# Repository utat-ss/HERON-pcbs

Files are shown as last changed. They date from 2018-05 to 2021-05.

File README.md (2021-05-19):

# Printed Circuit Boards (PCBs)

This repository houses Altium PCB designs for the Heron MK II CubeSat project. It contains [pcbs-common](https://github.com/HeronMkII/pcbs-common) as a Git submodule with commonly used schematics.

**Export all schematics and board layouts to PDF files so others can easily view them without using Altium.**

## How to add pcbs-common files into your current Altium project

- Update your GitHub with the pcbs-common submodule

- Run these git commands from your `./pcbs` folder:

```
git submodule init .
git submodule update --remote pcbs-common
```

- Get the files in your current project
- Project → Add Existing to Project → navigate to your copy of pcbs-common → select relevant files for your design.
- Substitute your current subsheets with the pcbs-common versions
- Open properties of target subsheet (the green box) → find the label indicating from where it’s taking the current subsheet → select the ... → navigate to the pcbs-common version in your project → select and OK
- Synchronize the labels to the subsheet with pcbs-common version
- Right click on the green box → sheet actions → synchronize sheet labels → select the pairs of corresponding sheet symbols → select the bottom arrow option (symbol of a beige box to a blue box [this pushes the version from pcbs-common onto the upper level]).
- When you run out of things to link, select the remaining items in the middle column → add (bottom option) → add no ERCs (X symbols) to pins you are not currently using.

## Updating pcbs-common

From the `pcbs` folder:

`$ git submodule update --remote`

This will fetch the latest commit of `pcbs-common` and update your files.

If you get an error about having modified files inside the `pcbs-common` folder, run the following:

```
$ cd pcbs-common
$ git reset --hard
```

This will discard all local changes you have made in the `pcbs-common` folder. Then, run `$ git submodule update --remote` again to download the most updated version of the `pcbs-common` files.

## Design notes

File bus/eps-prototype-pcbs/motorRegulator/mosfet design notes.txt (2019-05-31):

Vds max = 130 V (must be larger than Vout)
Ids max = 8 A
Rds max = 16.25 ohms
"In most applications, a logic level MOSFET can be used"

The critical parameters for selecting a MOSFET are:
1. Minimum threshold voltage, VTH(MIN)
2. On-resistance, RDS(ON)
3. Total gate charge, Qg
4. Reverse transfer capacitance, CRSS
5. Maximum drain to source voltage, VDS(MAX)

*The off-state voltage of the MOSFET is approximately equal to the output voltage*. Vds(max) must be greater
than the output voltage. The power losses in the MOSFET can be categorized into conduction losses and
switching losses

"The voltage on the drive pin, VDR is equal to the input voltage when input voltage is less than 7.2 V. 
VDR is equal to 7.2 V when the input voltage is greater than or equal to 7.2 V"

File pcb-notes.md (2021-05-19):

## Current PCBs in Lab (as of 2019-01-19)

### PAY-SSM

[Manufacturing notes](https://github.com/HeronMkII/pcbs/issues/14)

Programming PAY-SSM microcontroller:
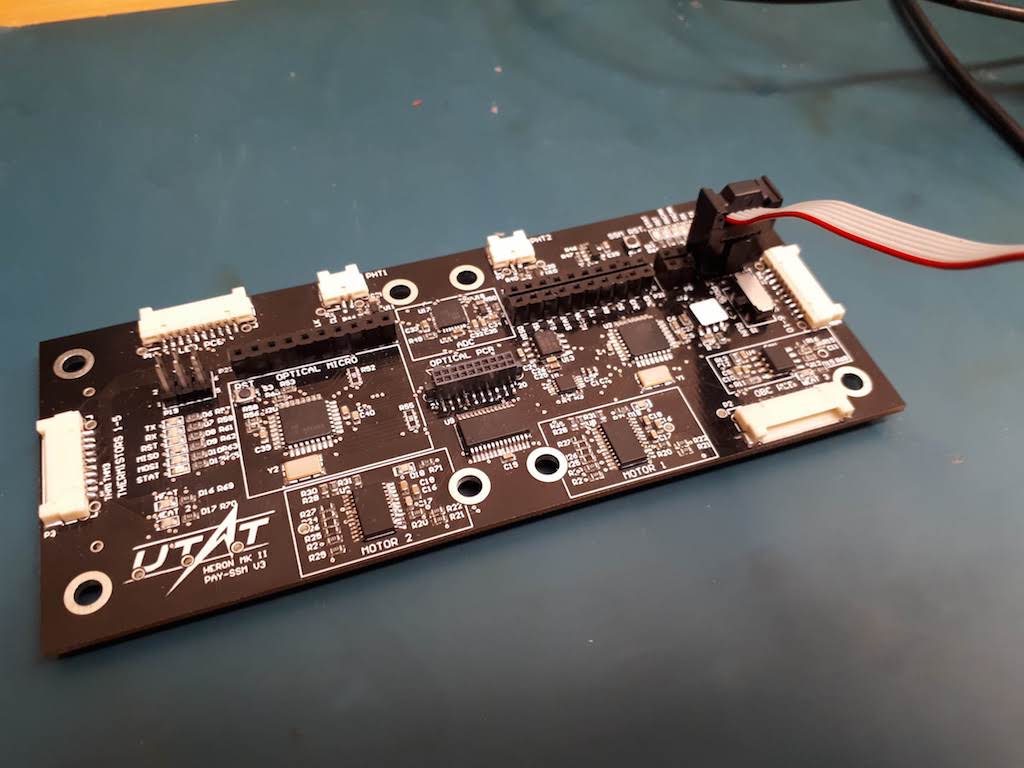
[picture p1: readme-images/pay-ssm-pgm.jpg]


Programming PAY-Optical microcontroller:
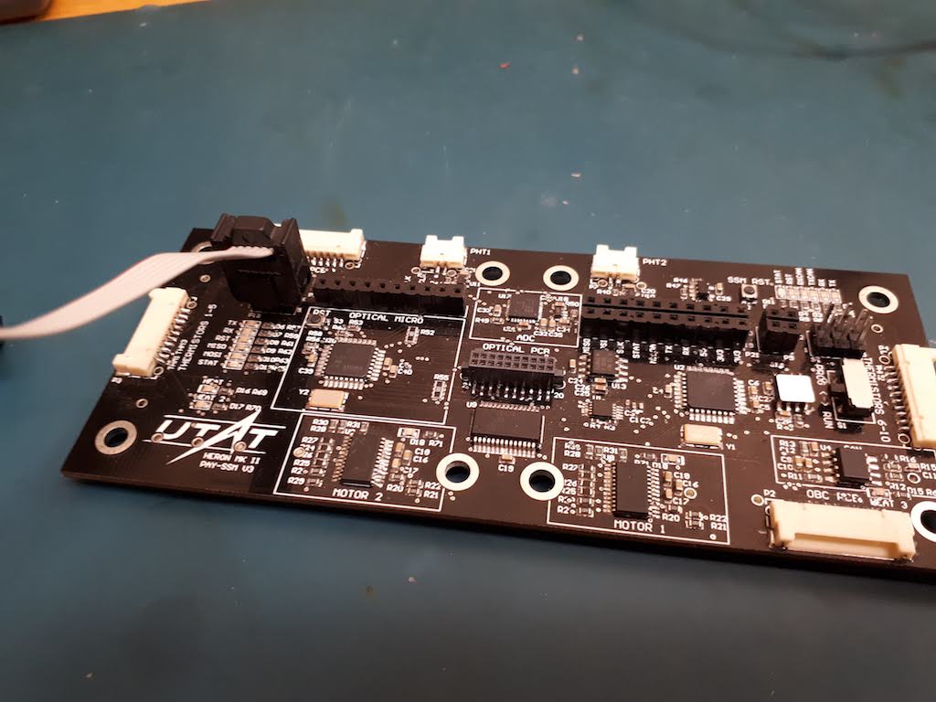
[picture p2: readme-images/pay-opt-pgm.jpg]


- **Programming headers - for both, the notch on the connector must face DOWN**
    - Board orientation is determined by the UTAT logo
- **Contains two microcontrollers:**
    - **PAY-SSM (right side)**
        - Controls SSM functions
        - Need to set switch to PROG when uploading programs, and RUN when executing programs
        - Switch must be in RUN mode for SSM_RST button and UART to work
        - Can leave microcontroller's RX pin connected when uploading a program (commands from a laptop)
    - **PAY-Optical (left side)**
        - Controls optical sensor setup
        - Should be on the PAY-Optical board, but is on the SSM board due to space constraints
        - UART headers (from MCU's perspective) - TX (DI, for printing, more common), RX (CLK, for commands, less common)
        - Need to disconnect RX (CLK) pin when uploading a program
- Payload subsystem main board
- Controls motors, heaters, thermistors
- Interfaces with EPS/OBC on the CAN bus
- 10-pin DF-14 connector to EPS
- 2x2 header on right side between long debugging header and programming header - top 2 pins are MCU's TX (prints), bottom 2 pins are MCU's RX (laptop commands)
- Careful of different 5V and 3V3 headers!!
- 5V supply required if using motors and heaters
- The two microcontrollers are connected to each other over SPI, where PAY-SSM functions as the master and PAY-Optical functions as the slave
- If the PAY-Optical MCU doesn't program properly, the PAY-SSM MCU might be interfering by sending SPI messages to it - either upload an empty program to the PAY-SSM MCU or hold down the SSM_RST button when programming the PAY-Optical MCU
- Disconnected (desoldered) CONFIG pin on both motor drivers so they use phase/enable mode

### PAY-Optical

[Manufacturing notes](https://github.com/HeronMkII/pcbs/issues/15)

Connecting PAY-SSM PCB to PAY-Optical PCB (if using 20-pin cable for debugging instead of stacking header pins):
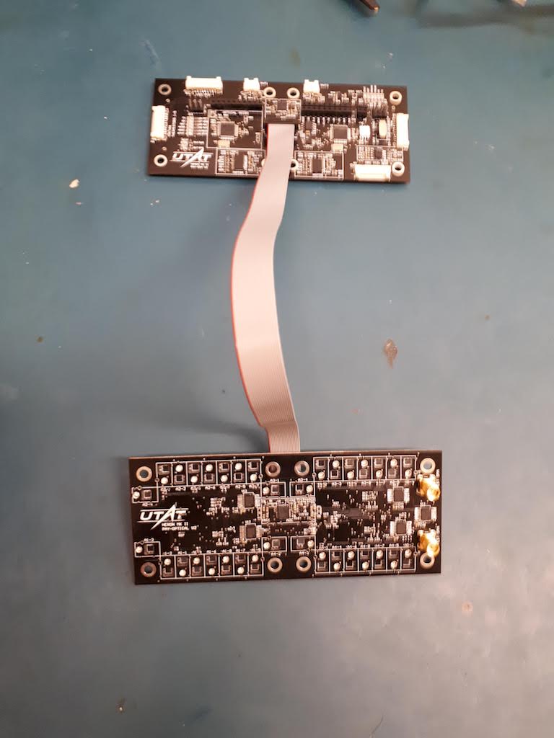
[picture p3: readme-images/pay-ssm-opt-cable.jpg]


- Payload optical board
- Physically stacked on top of PAY-SSM with a 20-pin header
    - Bought a 20-pin wire for testing without having to stack the boards
- 34 optical sensors and 2 SMA connectors to test input by simulating the input signal after the first amplification stage
- MCU for optical setup is located on the PAY-SSM PCB

### PAY-LED

[Manufacturing notes](https://github.com/HeronMkII/pcbs/issues/20)

- Payload LED board
- Contains LEDs on opposite side from PAY-Optical board
- Second copy currently (on 2018-09-18) being soldered by Cindy
- Each LED board has a 10-pin DF14 connector to PAY-SSM

### BUS (OBC/EPS/COMM)

- Combined onboard computer, electrical power systems, and communications on the same board
- Next iteration will have OBC on its own board, EPS/COMM still together on the other board
- Decided to not finish soldering a complete board with all components, just a couple of partially finished boards
- Connects to systems PCB with DSUB-25 connector
- Two MCUs: EPS and OBC
- Must program MCUs through the systems debug PCB

### Systems Debug PCB

- Systems debugging board
- Connects to EPS board with DSUB-25 connector
- Will allow us to plug in the single DSUB-25 cable to the satellite, program and view UART from any board/MCU, and monitor high-level debugging signals
- The following picture shows the v1 (on the left) and v2 (on the right) Systems Debug PCB. V2 has all the components soldered on and is ready to be used. Potential issues and changes are documented in Issue [#70](https://github.com/HeronMkII/pcbs/issues/70)
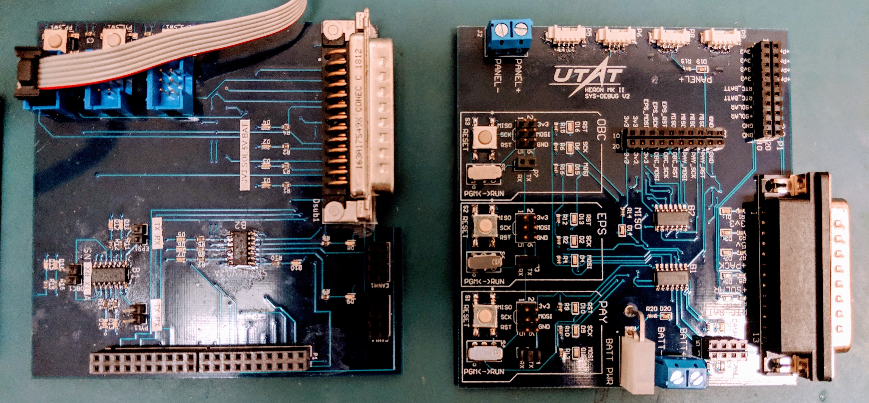
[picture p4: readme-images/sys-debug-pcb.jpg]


## Old PCBs in Lab

### OBC-001

### OBC-002

### PAY-SSM
- Not all components soldered
- Previously used to test conformal coating

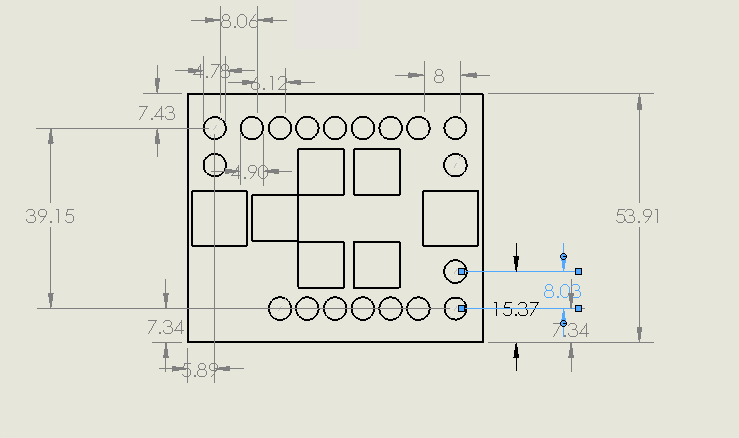
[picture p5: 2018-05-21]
payload/chip_dimensions_confusing.PNG

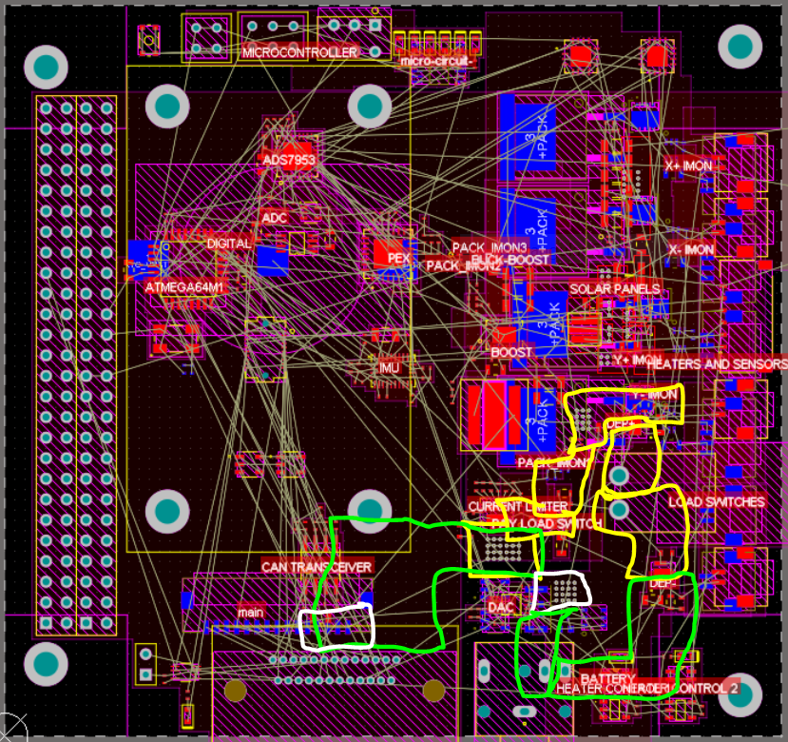
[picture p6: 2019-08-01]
bus/eps/EPS_batt_connector_layout.PNG

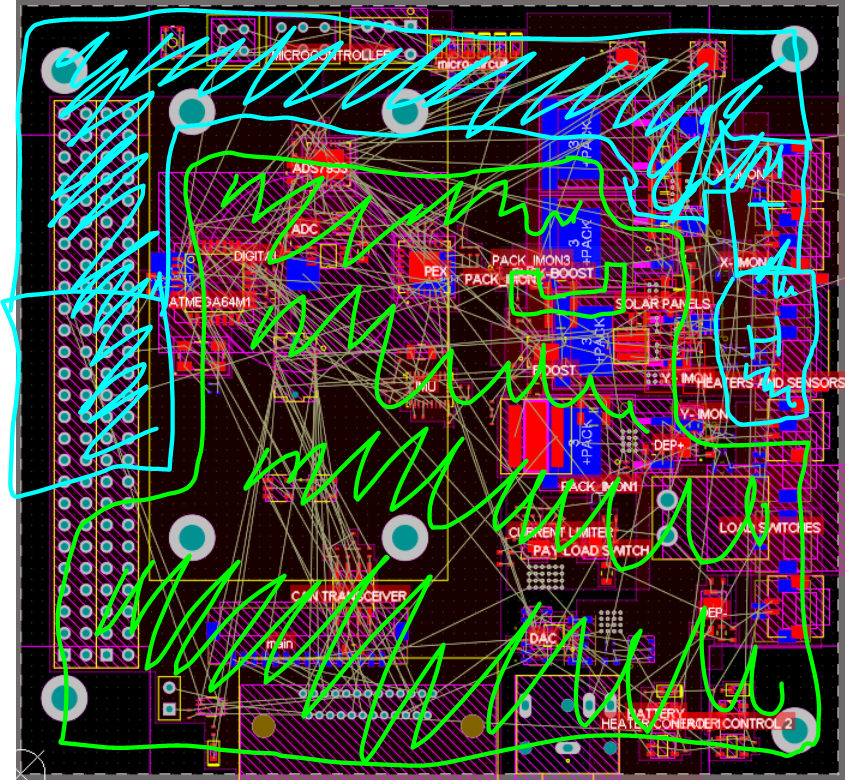
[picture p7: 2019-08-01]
bus/eps/EPS_converter_outputs.PNG

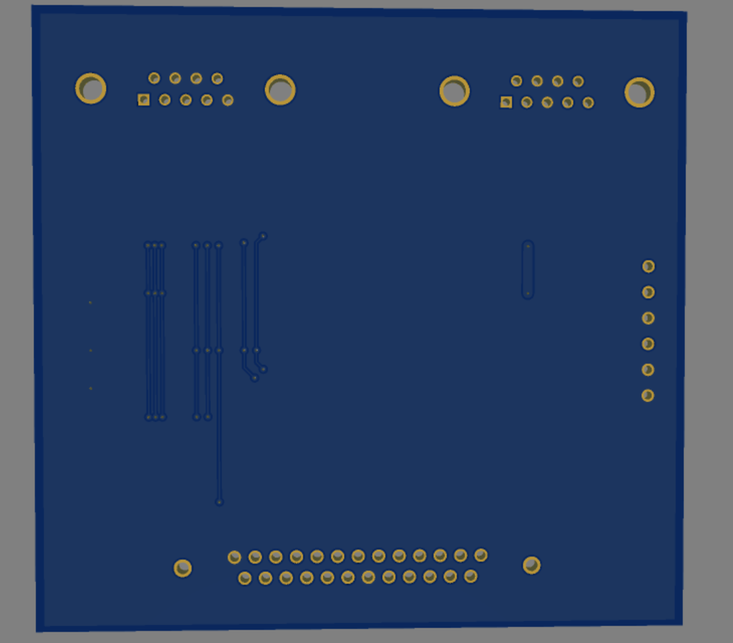
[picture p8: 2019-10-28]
systems/systems_interface_pcb/v4 TVAC System Interface PCB/render images/bottom.PNG

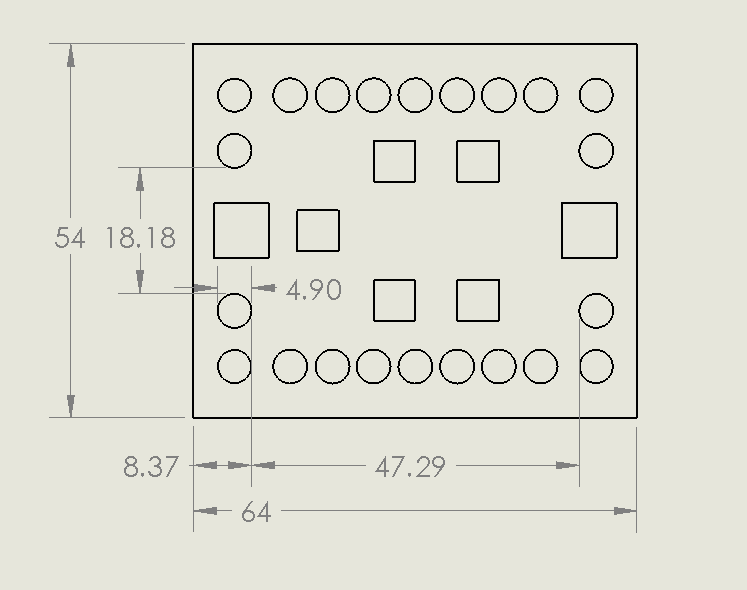
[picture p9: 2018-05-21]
payload/chip_dimensions_simple.PNG

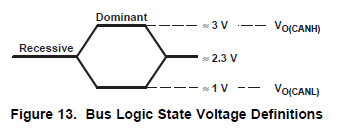
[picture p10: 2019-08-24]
systems/systems_pcb/can_transceiver_logic_voltages.PNG

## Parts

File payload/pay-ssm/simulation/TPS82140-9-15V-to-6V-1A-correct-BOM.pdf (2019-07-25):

## WEBENCH ® Design Report

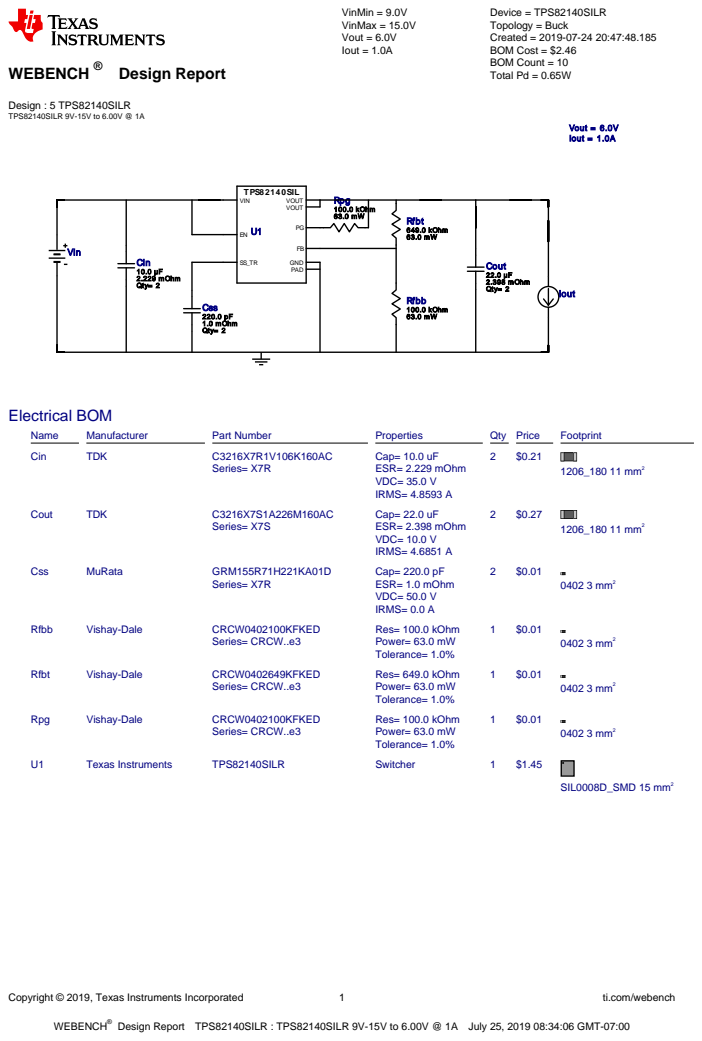
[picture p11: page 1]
Copyright © 2019, Texas Instruments Incorporated; ti.com/webench; WEBENCH®; Design : 5 TPS82140SILR TPS82140SILR 9V-15V to 6.00V @ 1A; VinMin = 9.0V VinMax = 15.0V Vout = 6.0V Iout = 1.0A; Device = TPS82140SILR Topology = Buck Created = 2019-07-24 20:47:48.185 BOM Cost = $2.46 BOM Count = 10 Total Pd = 0.65W; Cin 10.0 µF 2.229 mOhm Qty= 2; Cout 22.0 µF 2.398 mOhm Qty= 2; Css 220.0 pF 1.0 mOhm Qty= 2; Rfbb 100.0 kOhm 63.0 mW; Rfbt 649.0 kOhm 63.0 mW; Rpg 100.0 kOhm 63.0 mW; TPS82140SIL; VIN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

Design Report TPS82140SILR : TPS82140SILR 9V-15V to 6.00V @ 1A July 25, 2019 08:34:06 GMT-07:00

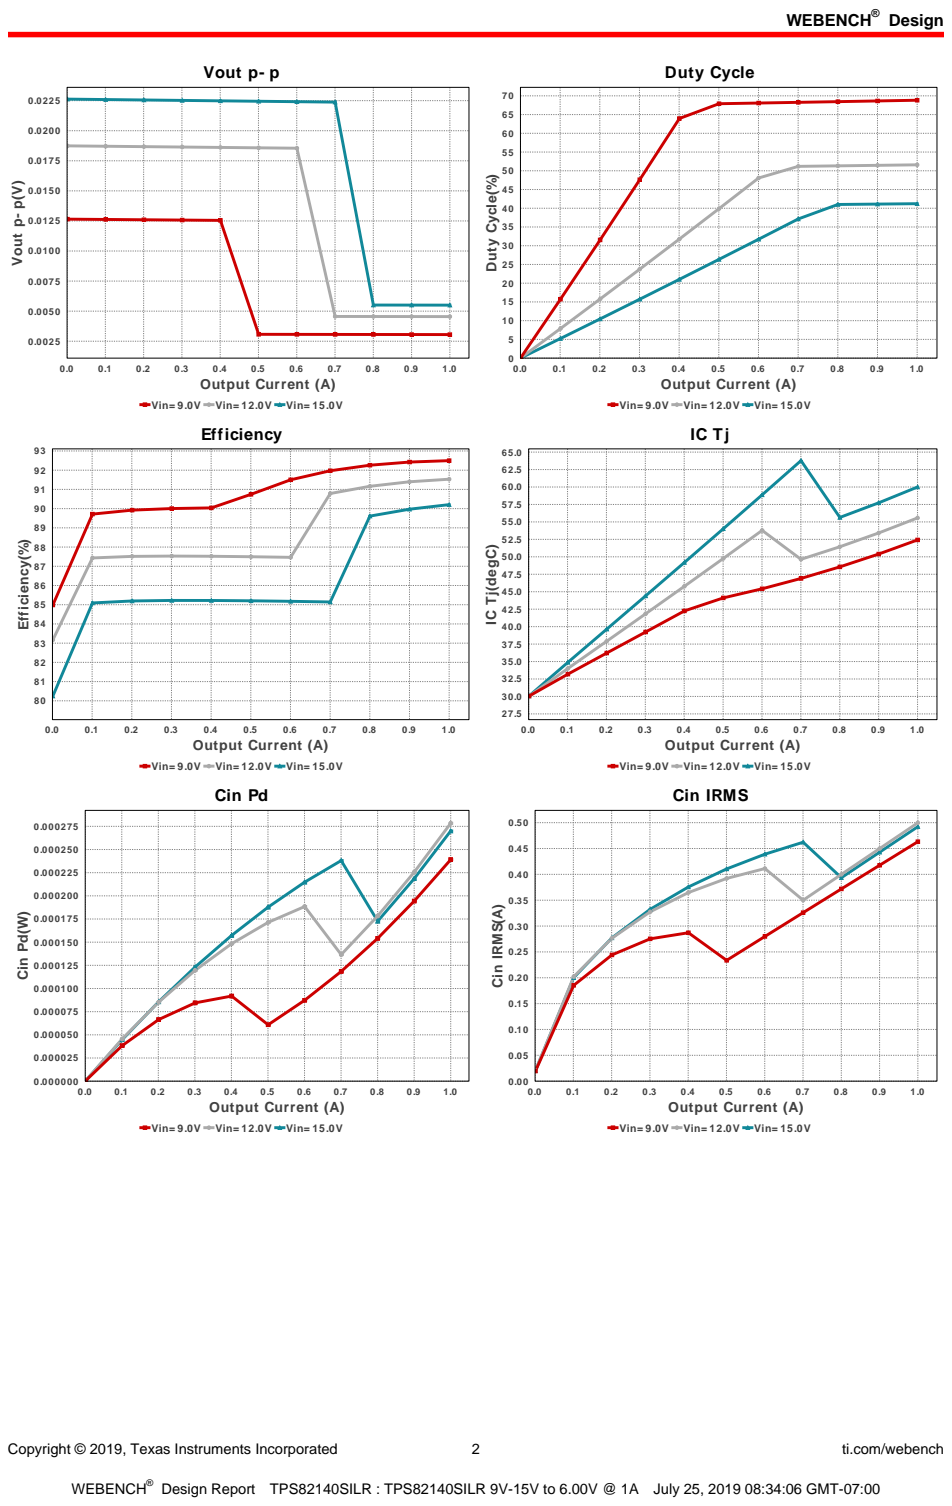
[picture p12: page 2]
Design; Copyright © 2019, Texas Instruments Incorporated; ti.com/webench; Vout p- p; 1.0 Output Current (A); Vout p- p(V); Duty Cycle; Duty Cycle(%); Efficiency(%); Cin Pd; Cin Pd(W); Cin IRMS(A)

Vin= 9.0V Vin= 12.0V Vin= 15.0V
Efficiency

IC Tj(degC)

Cin IRMS

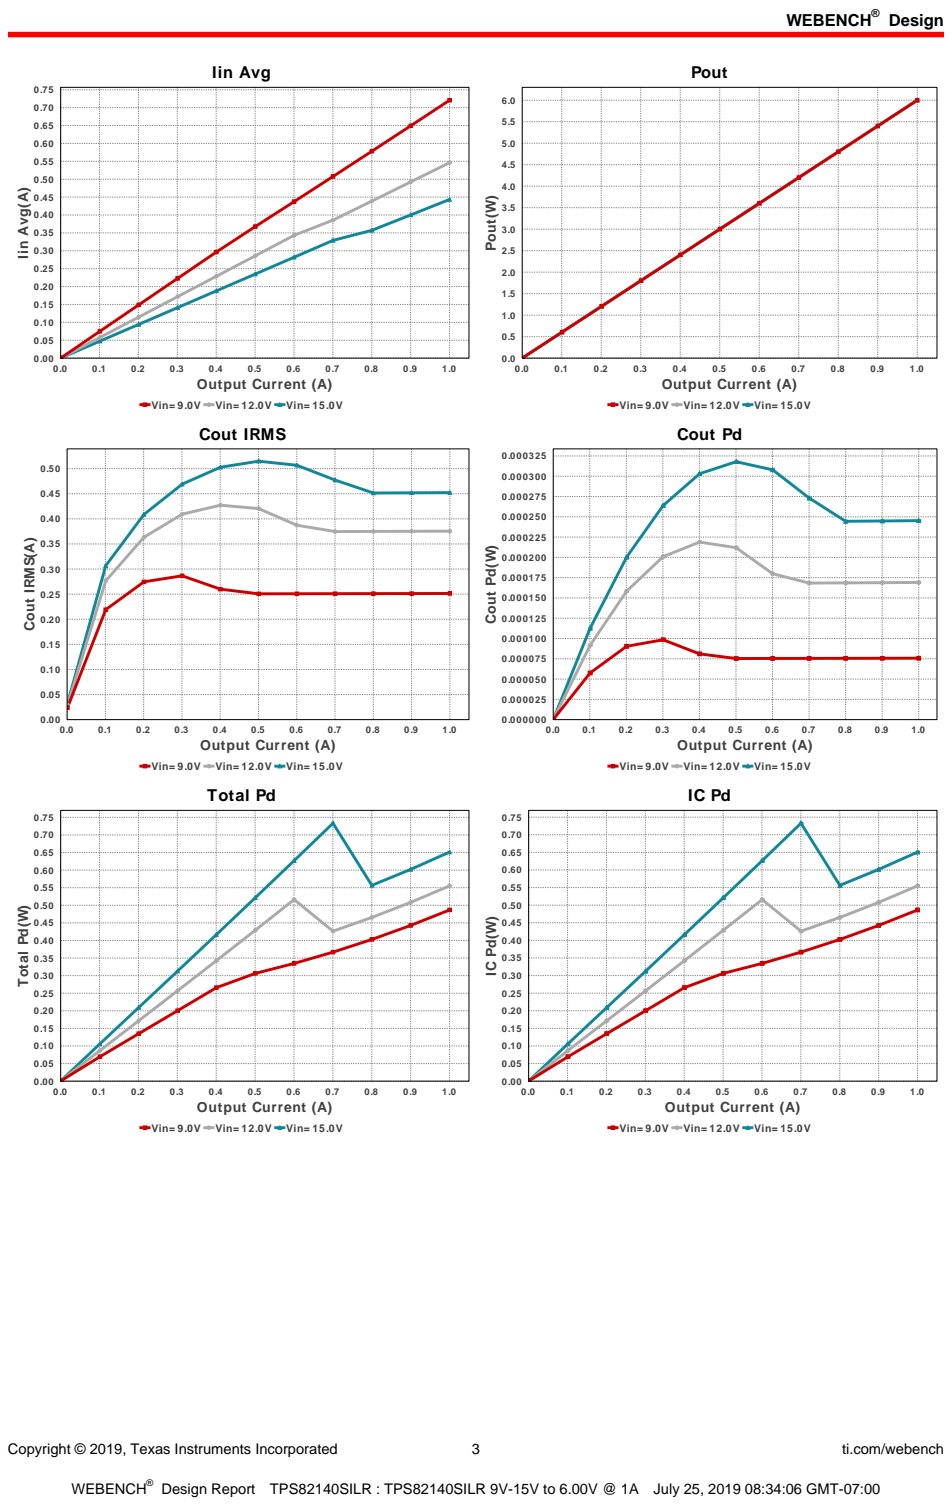
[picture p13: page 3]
Copyright © 2019, Texas Instruments Incorporated; ti.com/webench; Iin Avg; 1.0 Output Current (A); Iin Avg(A); Pout; Pout(W); Cout IRMS(A); Cout Pd(W); Total Pd(W)

Vin= 9.0V Vin= 12.0V Vin= 15.0V
Cout IRMS

Cout Pd

Total Pd

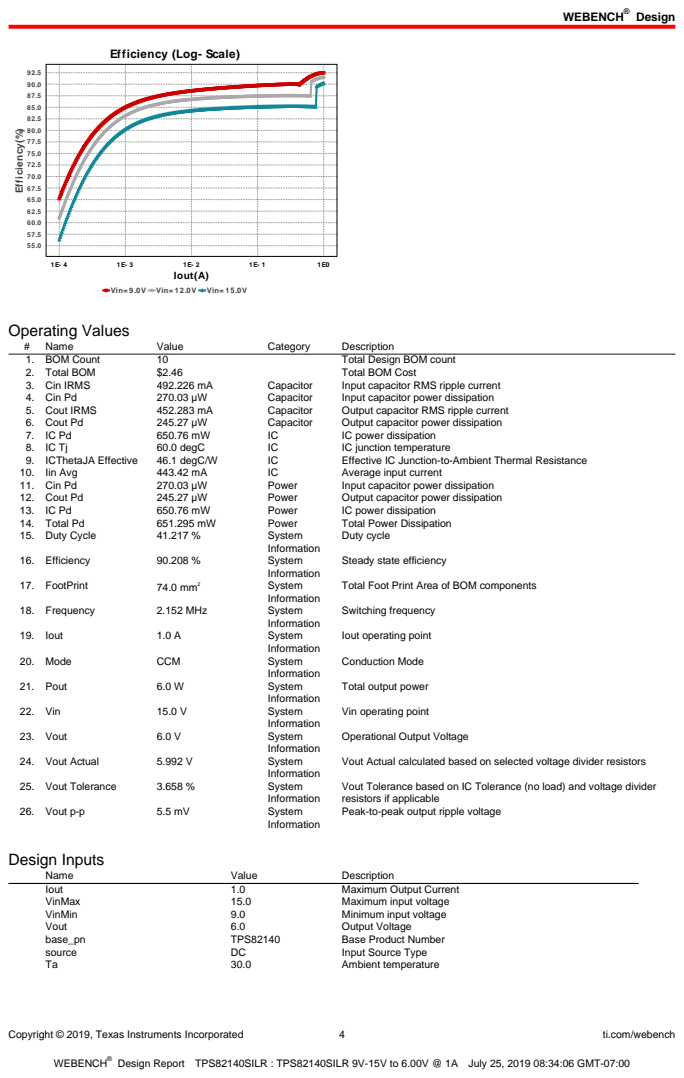
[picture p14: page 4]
Copyright © 2019, Texas Instruments Incorporated; ti.com/webench; Iout(A); Efficiency(%); Operating Values; Name; Value; Category; Description; 1. BOM Count; Total Design BOM count; 2. Total BOM; Total BOM Cost; 3. Cin IRMS; Capacitor; Input capacitor RMS ripple current; 4. Cin Pd; Input capacitor power dissipation; 5. Cout IRMS; Output capacitor RMS ripple current; 6. Cout Pd; Output capacitor power dissipation; IC power dissipation; 60.0 degC; IC junction temperature; 9. ICThetaJA Effective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

Efficiency (Log- Scale)

Vin= 9.0V Vin= 12.0V Vin= 15.0V

Steady state efficiency

Total Foot Print Area of BOM components

Iout operating point

Total output power

Vin operating point

Operational Output Voltage

Vout Actual calculated based on selected voltage divider resistors

Vout Tolerance based on IC Tolerance (no load) and voltage divider
resistors if applicable
Peak-to-peak output ripple voltage


Copyright © 2019, Texas Instruments Incorporated | 5 | ti.com/webench

## Assembly

## Component Testing

Some published data on components in datasheets such as Capacitor ESR and Inductor DC resistance is based on conservative values that will guarantee that the components always exceed the specification. For design purposes it is usually better to work with typical values. Since this data is not always available it is a good practice to measure the Capacitance and ESR values of Cin and Cout, and the inductance and DC resistance of L1 before assembly of the board. Any large discrepancies in values should be electrically simulated in WEBENCH to check for instabilities and thermally simulated in WebTHERM to make sure critical temperatures are not exceeded.

## Soldering Component to Board

If board assembly is done in house it is best to tack down one terminal of a component on the board then solder the other terminal. For surface mount parts with large tabs, such as the DPAK, the tab on the back of the package should be pre-tinned with solder, then tacked into place by one of the pins. To solder the tab town to the board place the iron down on the board while resting against the tab, heating both surfaces simultaneously. Apply light pressure to the top of the plastic case until the solder flows around the part and the part is flush with the PCB. If the solder is not flowing around the board you may need a higher wattage iron (generally 25W to 30W is enough).

## Initial Startup of Circuit

It is best to initially power up the board by setting the input supply voltage to the lowest operating input voltage 9.0V and set the input supply's current limit to zero. With the input supply off connect up the input supply to Vin and GND. Connect a digital volt meter and a load if needed to set the minimum Iout of the design from Vout and GND. Turn on the input supply and slowly turn up the current limit on the input supply. If the voltage starts to rise on the input supply continue increasing the input supply current limit while watching the output voltage. If the current increases on the input supply, but the voltage remains near zero, then there may be a short or a component misplaced on the board. Power down the board and visually inspect for solder bridges and recheck the diode and capacitor polarities. Once the power supply circuit is operational then more extensive testing may include full load testing, transient load and line tests to compare with simulation results.

## Load Testing

The setup is the same as the initial startup, except that an additional digital voltmeter is connected between Vin and GND, a load is connected between Vout and GND and a current meter is connected in series between Vout and the load. The load must be able to handle at least rated output power + 50% ( 7.5 watts for this design). Ideally the load is supplied in the form of a variable load test unit. It can also be done in the form of suitably large power resistors. When using an oscilloscope to measure waveforms on the prototype board, the ground leads of the oscilloscope probes should be as short as possible and the area of the loop formed by the ground lead should be kept to a minimum. This will help reduce ground lead inductance and eliminate EMI noise that is not actually present in the circuit.

## WEBENCH® Electrical Simulation Report

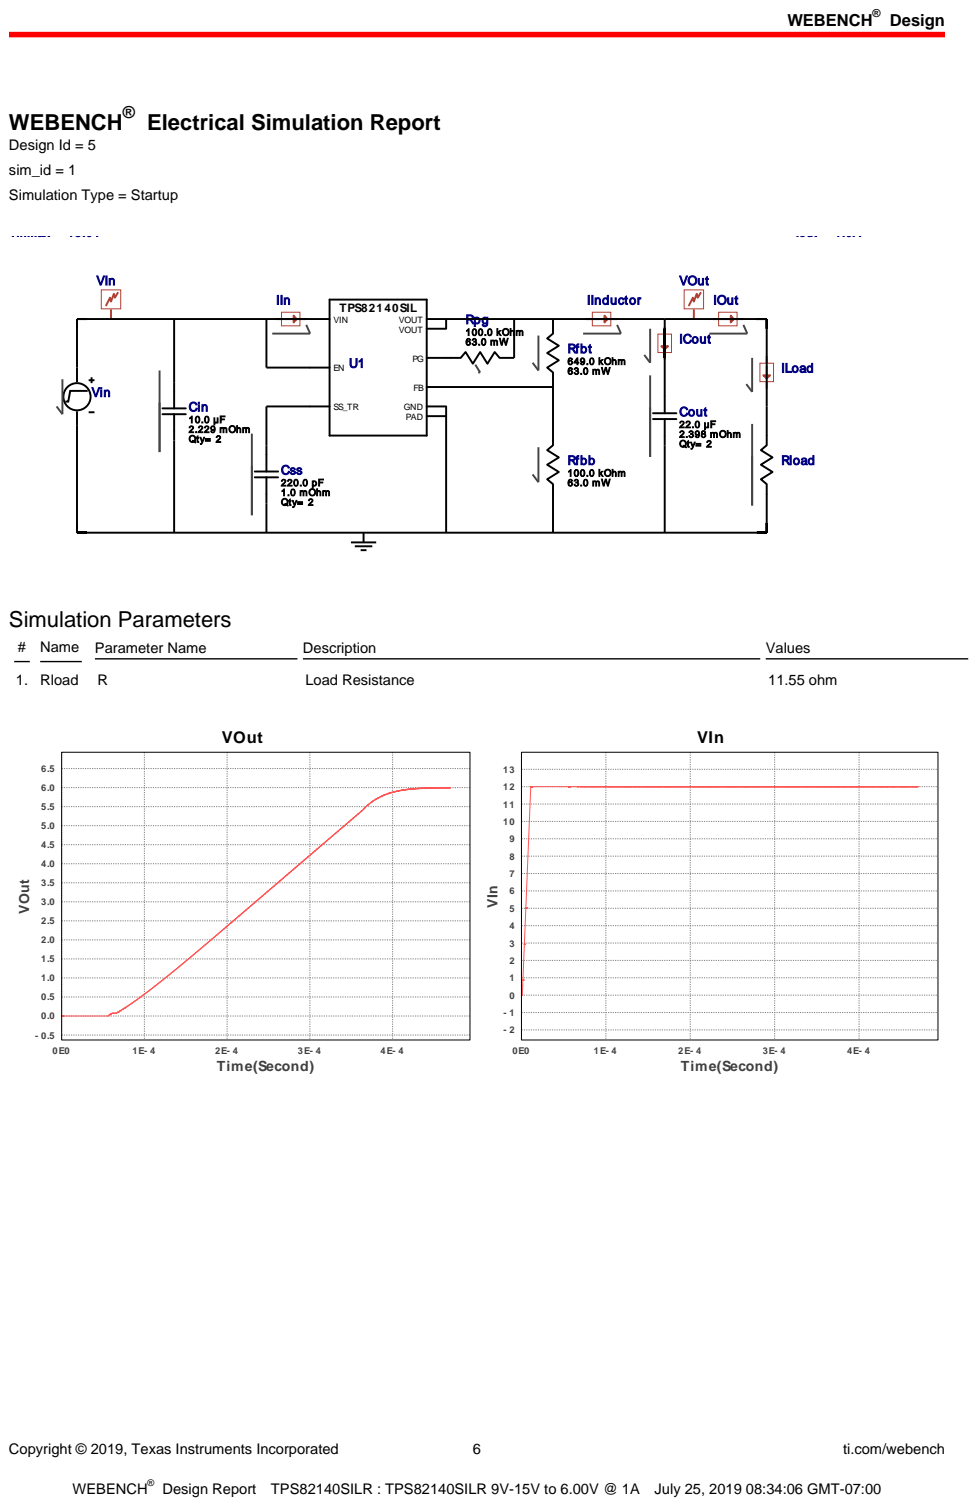
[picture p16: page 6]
Copyright © 2019, Texas Instruments Incorporated; ti.com/webench; Cin 10.0 µF 2.229 mOhm Qty= 2; Cout 22.0 µF 2.398 mOhm Qty= 2; Css 220.0 pF 1.0 mOhm Qty= 2; ICout; IIn; IInductor; IOut; Rfbb 100.0 kOhm 63.0 mW; Rfbt 649.0 kOhm 63.0 mW; Rpg 100.0 kOhm 63.0 mW; TPS82140SIL; VIN; GND; VOUT VOUT; PAD; VIn; VOut; Vin; ILoad; Rload; Simulation Parameters; # Name Parameter Name; Description; Values; 1. Rload R; Load Resistance; 11.55 ohm; 4E- 4 Time(Second)

Design Id = 5
sim_id = 1
Simulation Type = Startup

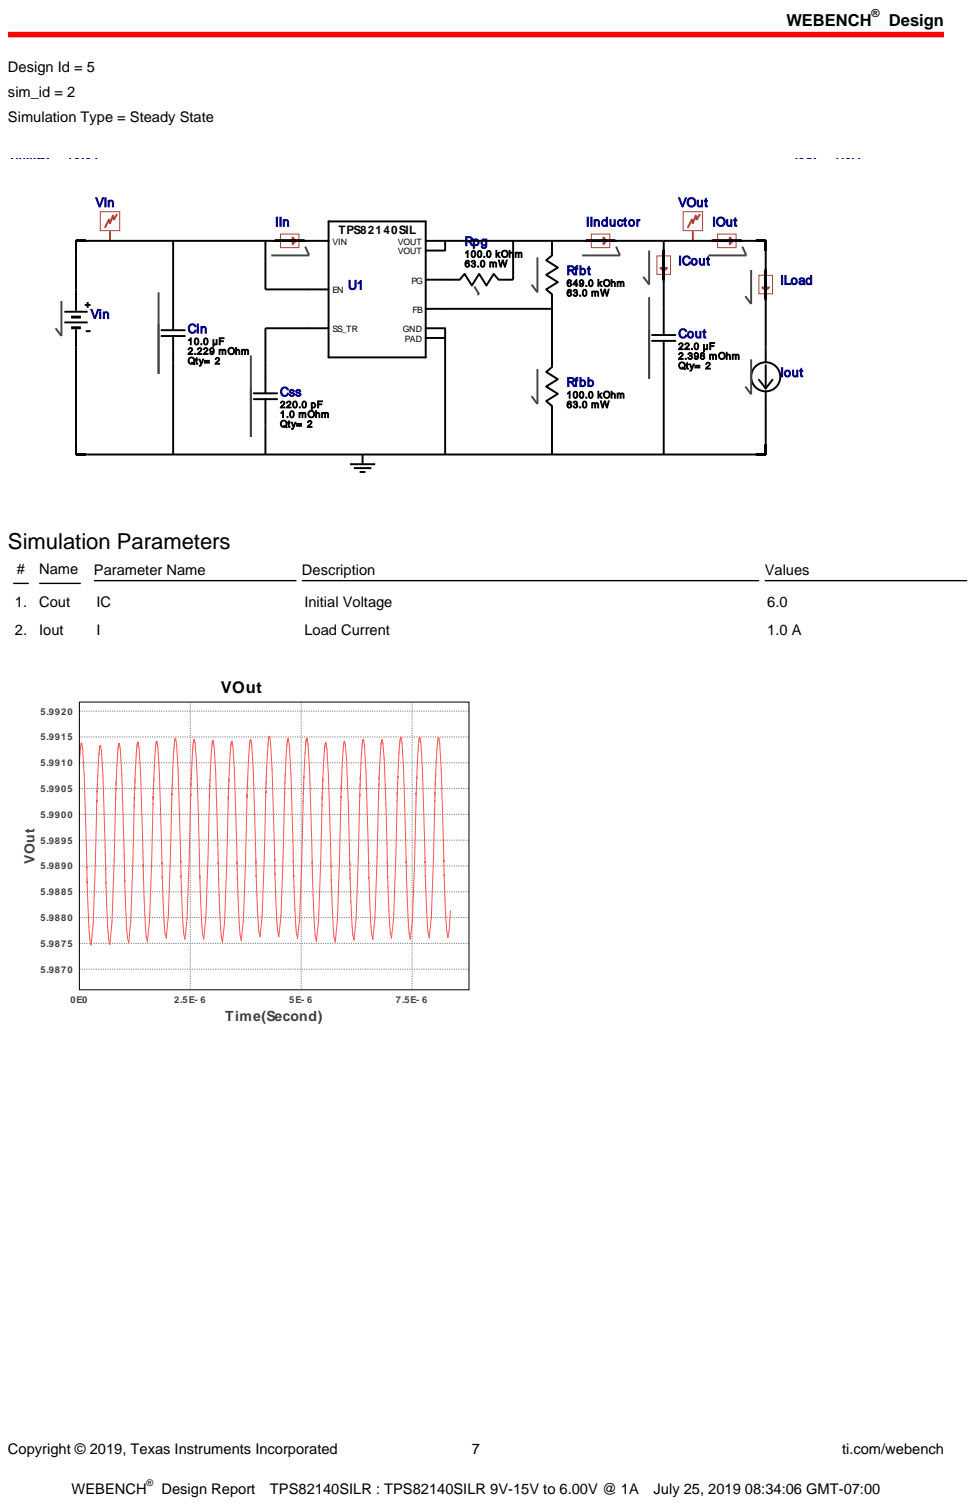
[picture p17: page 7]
Copyright © 2019, Texas Instruments Incorporated; ti.com/webench; Cin 10.0 µF 2.229 mOhm Qty= 2; Cout 22.0 µF 2.398 mOhm Qty= 2; Css 220.0 pF 1.0 mOhm Qty= 2; ICout; IIn; IInductor; IOut; Rfbb 100.0 kOhm 63.0 mW; Rfbt 649.0 kOhm 63.0 mW; Rpg 100.0 kOhm 63.0 mW; TPS82140SIL; VIN; GND; VOUT VOUT; PAD; VIn; VOut; Vin; ILoad; Iout; Simulation Parameters; # Name Parameter Name; Description; Values; 1. Cout; Initial Voltage; 2. Iout; Load Current; 7.5E- 6 Time(Second)

Design Id = 5
sim_id = 2
Simulation Type = Steady State

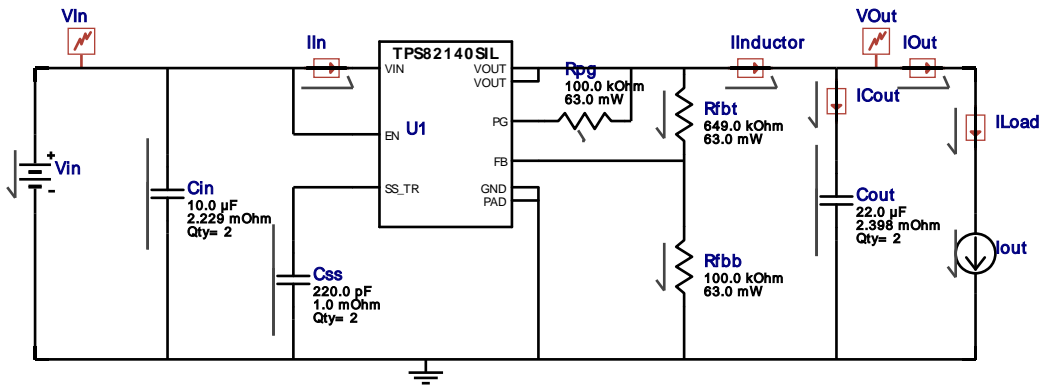
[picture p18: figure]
Cin 10.0 µF 2.229 mOhm Qty= 2; Cout 22.0 µF 2.398 mOhm Qty= 2; Css 220.0 pF 1.0 mOhm Qty= 2; ICout; IIn; IInductor; IOut; Rfbb 100.0 kOhm 63.0 mW; Rfbt 649.0 kOhm 63.0 mW; Rpg 100.0 kOhm 63.0 mW; TPS82140SIL; VIN; GND; VOUT VOUT; PAD; VIn; VOut; Vin; ILoad; Iout

Copyright © 2019, Texas Instruments Incorporated | 8 | ti.com/webench

Design Id = 5
sim_id = 3
Simulation Type = Steady State

## Simulation Parameters

# Name Parameter Name | Description | Values

1. Cout | IC | Initial Voltage | 6.0
2. Iout | I | Load Current | 0.541 A

VOut

0E0 | 1E- 6 | 2E- 6 | 3E- 6 | 4E- 6 | 5E- 6 | 6E- 6 | 7E- 6 | 8E- 6 Time(Second)

5.9860

5.9865

5.9870

5.9875

5.9880

5.9885

5.9890

5.9895

5.9900

5.9905

5.9910

5.9915

5.9920

5.9925

5.9930

VOut

## Design Assistance

1. Feature Highlights: DCS-Control(TM) Architecture with up to 3A output current, Power module with integrated inductor, 3V to 17V Input Voltage Range, Adjustable output voltage from 0.9V to 5V, Optional softstart capacitor for slow startup, Power Save Mode for light load efficiency, 100% duty cycle for lowest dropout, PG=Low when device is in shutdown through EN or Thermal Shutdown
2. Master key : 84F8F281898B6F10[v1]
3. TPS82140 Product Folder : http://www.ti.com/product/TPS82140 : contains the data sheet and other resources.

Copyright © 2019, Texas Instruments Incorporated | 9 | ti.com/webench

Important Notice and Disclaimer

TI provides technical and reliability data (including datasheets), design resources (including reference designs), application or other design advice, web tools, safety information, and other resources AS IS and with all faults, and disclaims all warranties. These resources are intended for skilled developers designing with TI products. You are solely responsible for (1) selecting the appropriate TI products for your application, (2) designing, validating and testing your application, and (3) ensuring your application meets applicable standards, and any other safety, security, or other requirements.

These resources are subject to change without notice. TI grants you permission to use these resources only for development of an application that uses the TI products described in the resource. Other reproduction and display of these resources is prohibited. No license is granted to any other TI intellectual property right or to any third party intellectual property right. TI disclaims responsibility for, and you will fully indemnify TI and its representatives against, any claims, damages, costs, losses, and liabilities arising out of your use of these resources.

Providing these resources does not expand or otherwise alter TI's applicable Terms of Sale or other applicable terms available either on ti.com or provided in conjunction with TI products.

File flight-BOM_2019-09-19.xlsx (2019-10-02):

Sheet: pay-ssm
Line # | Name | Designator | Value | Quantity | Supplier 1 | Supplier Part Number 1 | Supplier Unit Price 1 | Supplier Subtotal 1
 | 2A 0402 | L4 | 120 Ohm @ 100MHz | 1 | Digi-Key | 490-16505-1-ND | 0.19869 | 0.19869
 | 8MHz Crystal | Y1 |  | 1 | Digi-Key | 535-13456-1-ND | 1.51 | 1.51
 | 402 | C2, C3, C4, C8, C10_ADC1, C10_ADC2, C45_Port_Expander1, C45_Port_Expander2, C46_Current_Monitor1, C46_Current_Monitor2, C56 | 0.1uF | 11 | Digi-Key | 587-3807-6-ND | 0.09124 | 1
 | 402 | C5, C6 | 22pF | 2 | Digi-Key | 399-17554-1-ND | 0.25168 | 0.50335
 | 402 | C9 | 47pF | 1 | Digi-Key | 399-17558-1-ND | 0.1722 | 0.1722
 | 402 | C11_ADC1, C11_ADC2 | 220pF | 2 | Digi-Key | 490-4912-1-ND | 0.13246 | 0.26492
 | 402 | C20, C30, C31, C32, C42, C44, C52 | 0.1uF 16V X7R | 7 | Digi-Key | 587-3807-6-ND | 0.09124 | 0.91239
 | 402 | C26 | 820pF 50V X7R | 1 | Digi-Key | 490-3250-1-ND | 0.13246 | 0.13246
 | 402 | C27, C49 | 8.2nF 16V X7R | 2 | Digi-Key | 490-6338-1-ND | 0.13246 | 0.26492
 | 402 | C29 | 39pF 25V C0G | 1 | Digi-Key | 490-6178-1-ND | 0.13246 | 0.13246
 | 402 | C36_MOTOR_DRV1, C36_MOTOR_DRV2, C53 | 10000pF | 3 | Digi-Key | 490-4762-1-ND | 0.13246 | 0.39738
 | 402 | C43 | 0.22uF 6.3V X7R | 1 | Digi-Key | 587-3764-6-ND | 0.14571 | 0.14571
 | 402 | C48 | 560pF 50V X7R | 1 | Digi-Key | 490-1301-1-ND | 0.13246 | 0.13246
 | 402 | C51 | 27pF 50V C0G | 1 | Digi-Key | 490-5869-1-ND | 0.13246 | 0.13246
 | 402 | R1, R2, R17, R18, R27, R31, R40, R69_Port_Expander1, R69_Port_Expander2, R70_Port_Expander1, R70_Port_Expander2, R71_Port_Expander1, R71_Port_Expander2, R72_Port_Expander1, R72_Port_Expander2, R73_Port_Expander1, R73_Port_Expander2, R74_Port_Expander1, R74_Port_Expander2, R90 | 0 | 20 | Digi-Key | P0.0JCT-ND | 0.02861 | 0.71529
 | 402 | R4, R5, R6, R8, R9, R10, R13, R14, R15, R19_ADC1, R19_ADC2, R20_ADC1, R20_ADC2, R21_ADC1, R21_ADC2, R22_ADC1, R22_ADC2, R23_ADC1, R23_ADC2 | 100 | 19 | Digi-Key | 541-100YDKR-ND | 0.1828 | 3.47
 | 402 | R11 | 30K | 1 | Digi-Key | YAG3474CT-ND | 0.13246 | 0.13246
 | 402 | R12, R16 | 60.4 | 2 | Digi-Key | 541-60.4LCT-ND | 0.13246 | 0.26492
 | 402 | R24_ADS79521, R24_ADS79522, R44, R45, R46, R47, R48_MOTOR_DRV1, R48_MOTOR_DRV2, R51_MOTOR_DRV1, R51_MOTOR_DRV2, R52_MOTOR_DRV1, R52_MOTOR_DRV2, R53_MOTOR_DRV1, R53_MOTOR_DRV2, R58_MOTOR_DRV1, R58_MOTOR_DRV2, R59_MOTOR_DRV1, R59_MOTOR_DRV2, R60_MOTOR_DRV1, R60_MOTOR_DRV2, R61_MOTOR_DRV1, R61_MOTOR_DRV2, R66_HEATER1, R66_HEATER2, R66_HEATER3, R66_HEATER4, R66_HEATER5, R67_Port_Expander1, R67_Port_Expander2, R68_Port_Expander1, R68_Port_Expander2, R75, R77, R79 | 10K | 34 | Digi-Key | P10.0KLCT-ND | 0.05961 | 2.03
 | 402 | R30 | 453K 1% | 1 | Digi-Key | 541-453KLCT-ND | 0.13246 | 0.13246
 | 402 | R32 | 3K 1% | 1 | Digi-Key | RMCF0402FT3K00CT-ND | 0.13246 | 0.13246
 | 402 | R33 | 44.2K 1% | 1 | Digi-Key | P44.2KLCT-ND | 0.13246 | 0.13246
 | 402 | R35, R49_MOTOR_DRV1, R49_MOTOR_DRV2, R65_HEATER1, R65_HEATER2, R65_HEATER3, R65_HEATER4, R65_HEATER5, R94, R96_HEATER1, R96_HEATER2, R96_HEATER3, R96_HEATER4, R96_HEATER5, R99 | 1K | 15 | Digi-Key | 311-1.0KJRCT-ND | 0.01722 | 0.2583
 | 402 | R36, R41, R42, R43, R76 | 10K NTC | 5 | Digi-Key | P12007CT-ND | 0.19869 | 0.99346
 | 402 | R39 | 69.8K 1% | 1 | Digi-Key | 541-69.8KLCT-ND | 0.13246 | 0.13246
 | 402 | R50_MOTOR_DRV1, R50_MOTOR_DRV2 | 200 1% | 2 | Digi-Key | P200JCT-ND | 0.13246 | 0.26492
 | 402 | R62_MOTOR_DRV1, R62_MOTOR_DRV2, R63_MOTOR_DRV1, R63_MOTOR_DRV2, R97, R98 | 50K 1% | 6 | Digi-Key | P49.9KLCT-ND | 0.05961 | 0.59607
 | 402 | R64_MOTOR_DRV1, R64_MOTOR_DRV2, R80, R81, R82, R83, R84, R85 | 330 | 8 | Digi-Key | A129621CT-ND | 0.02914 | 0.29141
 | 402 | R78_Boost2_Temperature, R78_Boost_Temp_Sense, R78_General_Temp_Sense, R78_MF_THM1_6, R78_MF_THM1_7, R78_MF_THM1_8, R78_MF_THM1_9, R78_MF_THM1_10, R78_MF_THM1_11, R78_MF_THM2_12, R78_MF_THM2_13, R78_MF_THM2_14, R78_MF_THM2_15, R78_MF_THM2_16, R78_MF_THM2_17, R78_MOTOR_TEMP11, R78_MOTOR_TEMP12 | 10K 0.1% | 17 | Digi-Key | P10KDCCT-ND | 0.4252 | 7.23
 | 402 | R88 | 187K 1% | 1 | Digi-Key | P187KLCT-ND | 0.13246 | 0.13246
 | 402 | R91 | 1.4K 1% | 1 | Digi-Key | YAG3039DKR-ND | 0.13246 | 0.13246
 | 402 | R92 | 15.4K 1% | 1 | Digi-Key | YAG2992DKR-ND | 0.13246 | 0.13246
 | 402 | R93 | 118K 1% | 1 | Digi-Key | 541-118KLCT-ND | 0.13246 | 0.13246
 | 402 | R95 | 2 | 1 | Digi-Key | YAG3472CT-ND | 0.13246 | 0.13246
 | 402 | R100 | 2.2K 1% | 1 | Digi-Key | 311-2.20KLRDKR-ND | 0.13246 | 0.13246
 | 603 | C13_ADC1, C13_ADC2, C15_ADS79521, C15_ADS79522, C16_ADS79521, C16_ADS79522, C17_ADS79521, C17_ADS79522 | 1uF | 8 | Digi-Key | 399-17704-1-ND | 0.14438 | 1.44
 | 603 | C19 | 0.1uF 50V X7R | 1 | Digi-Key | 445-5666-1-ND | 0.13246 | 0.13246
 | 603 | C40_MOTOR_DRV1, C40_MOTOR_DRV2 | 2.2uF 6.3V X7R | 2 | Digi-Key | 445-6933-1-ND | 0.35764 | 0.71529
 | 603 | C54 | 1uF | 1 | Digi-Key | 399-17704-1-ND | 0.19869 | 0.19869
 | 603 | L1 | 10uH | 1 | Digi-Key | 445-17067-1-ND | 0.29141 | 0.29141
 | 603 | R3, R7, R25, R37, R38, R86 | 0 26A | 6 | Digi-Key | 2019-TLRZ1JTTDCT-ND | 0.82126 | 4.93
 | 603 | R34 | 62K 1% | 1 | Digi-Key | 311-62.0KHRCT-ND | 0.13246 | 0.13246
 | 603 | R89 | 470K 1% | 1 | Digi-Key | 311-470KHRCT-ND | 0.13246 | 0.13246
 | 805 | C1, C7, C12_ADC1, C12_ADC2, C18_ADS79521, C18_ADS79522, C41_Port_Expander1, C41_Port_Expander2, C55 | 10uF | 9 | Digi-Key | 490-14361-1-ND | 0.50883 | 5.09
 | 805 | C14_ADC1, C14_ADC2 | 10uF 1-1.5 ESR | 2 | Digi-Key | 490-14361-1-ND | 0.73693 | 1.47
 | 805 | C25, C47 | 2.2uF 16V X7R | 2 | Digi-Key | 490-3906-1-ND | 0.42388 | 0.84775
 | 805 | C35, C50 | 15uF 35V X5R | 2 | Digi-Key | 445-11470-1-ND | 0.8345 | 1.67
 | 805 | R26 | 215K 1% | 1 | Digi-Key | P215KCCT-ND | 0.13246 | 0.13246
 | 805 | R28, R87 | 8m 1% 1/2W | 2 | Digi-Key | RHM.008AJCT-ND | 0.861 | 1.72
 | 805 | R29 | 102K 1% | 1 | Digi-Key | 541-102KCCT-ND | 0.13246 | 0.13246
 | 805 | R54_MOTOR_DRV1, R54_MOTOR_DRV2, R55_MOTOR_DRV1, R55_MOTOR_DRV2, R56_MOTOR_DRV1, R56_MOTOR_DRV2, R57_MOTOR_DRV1, R57_MOTOR_DRV2 | 0.2 1% 1/4W | 8 | Digi-Key | WSLA-.20CT-ND | 1.03 | 8.27
 | 1206 | C22, C23 | 10uF 50V X5R | 2 | Digi-Key | 445-5998-1-ND | 1.28 | 2.57
 | 1206 | C33, C34 | 33uF 25V X5R | 2 | Digi-Key | 445-8046-1-ND | 1.59 | 3.18
 | 1206 | C37_MOTOR_DRV1, C37_MOTOR_DRV2, C38_MOTOR_DRV1, C38_MOTOR_DRV2, C39_MOTOR_DRV1, C39_MOTOR_DRV2 | 10uF 25V | 6 | Digi-Key | 445-174428-1-ND | 1.14 | 6.83
 | 2220 | C21, C24, C28 | 22uF 25V X7R | 3 | Digi-Key | 445-7934-1-ND | 3.42 | 10.25
 | AD8613 | U3_ADC1, U3_ADC2 |  | 2 | Digi-Key | AD8613AKSZ-REEL7CT-ND | 1.81 | 3.63
 | ADS7952 | U5_ADS79521, U5_ADS79522 |  | 2 | Digi-Key | 296-25842-1-ND | 12.16 | 24.32
 | ATMEGA64M1 | U1 |  | 1 | Digi-Key | ATMEGA64M1-AU-ND | 7.11 | 7.11
 | DF13A-2P-1.25H(21) | J7, J8, J9, J10, J11_HEATER1, J11_HEATER2, J11_HEATER3, J11_HEATER4, J11_HEATER5 |  | 9 | Digi-Key | H125743CT-ND | 0.56958 | 5.13
 | DF13A-4P-1.25H(51) | J5, J6 |  | 2 | Digi-Key | H125779CT-ND | 1.31 | 2.62
 | DF13A-12P-1.25H(51) | J12, J13 |  | 2 | Digi-Key | H125987CT-ND | 2.24 | 4.48
 | DF13A-15P-1.25H(21) | J1 |  | 1 | Digi-Key | H125988CT-ND | 1.6 | 1.6
 | DRV8834 | U7_MOTOR_DRV1, U7_MOTOR_DRV2 |  | 2 | Digi-Key | 296-41246-1-ND | 3.66 | 7.31
 | HIH7131 | U14 |  | 1 | Digi-Key | 480-5705-1-ND | 16.37 | 16.37
 | IHLP-1212BZ | L3 |  | 1 | Digi-Key | 541-1319-1-ND | 1.92 | 1.92
 | INA214CQDCKRQ1 | U8_Current_Monitor1, U8_Current_Monitor2 |  | 2 | Digi-Key | 296-51151-1-ND | 2.27 | 4.53
 | LED0603 | D1_MOTOR_DRV1, D1_MOTOR_DRV2, D2, D3, D4, D5, D6, D7, D8_HEATER1, D8_HEATER2, D8_HEATER3, D8_HEATER4, D8_HEATER5 |  | 13 | Digi-Key | 475-2816-6-ND | 0.40351 | 5.25
 | MCP23S17-QFN | U6_Port_Expander1, U6_Port_Expander2 |  | 2 | Digi-Key | MCP23S17T-E/MLCT-ND | 2.07 | 4.13
 | N-MOS | Q1_HEATER1, Q1_HEATER2, Q1_HEATER3, Q1_HEATER4, Q1_HEATER5, Q2_HEATER1, Q2_HEATER2, Q2_HEATER3, Q2_HEATER4, Q2_HEATER5 |  | 10 | Digi-Key | FDC637BNZCT-ND | 0.40533 | 4.05
 | REF5025 | U4_ADC1, U4_ADC2 |  | 2 | Digi-Key | 296-41382-1-ND | 3.97 | 7.95
 | SFMC-110-02-L-D | J2 |  | 1 | Digi-Key | SAM10120-ND | 5.34 | 5.34
 | SLW-102-01-G-D | J4 |  | 1 | Digi-Key | SAM1088-02-ND | 1.02 | 1.02
 | SLW-107-01-G-D | J14 |  | 1 | Digi-Key | SAM1088-07-ND | 3.02 | 3.02
 | SN65HVD233D | U2 |  | 1 | Digi-Key | 296-14639-5-ND | 4.15 | 4.15
 | SN74HC365PW | U11 |  | 1 | Digi-Key | 296-33932-5-ND | 0.88749 | 0.88749
 | SW-PB | S2 |  | 1 | Digi-Key | CKN10587CT-ND | 0.67555 | 0.67555
 | TPS61088 | BT1, BT2 |  | 2 | Digi-Key | 296-42129-1-ND | 5.85 | 11.71
 | DPDT | S1 |  | 1 | Mouser | 611-JS202011AQN | 0.59607 | 0.59607
 | MS5803-05BA | U16 |  | 1 | Mouser | 824-MS580305BA01-00 | 28.9 | 28.9
 | SLW-103-01-G-D | J3 |  | 1 | Mouser | 200-SLW10301GD | 1.62 | 1.62
 | XAL6020-112MEB | L2 | 1.1uH 20% 12A | 1 | Mouser | 994-XAL6020-112MEB | 2.81 | 2.81

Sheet: obc
Line # | Name | Description | Designator | Quantity | Manufacturer 1 | Manufacturer Part Number 1 | Manufacturer Lifecycle 1 | Supplier 1 | Supplier Part Number 1 | Supplier Unit Price 1 | Supplier Subtotal 1
 | LED0603 | Generic 0603 LED. Use ChipLED from Osram for generic ones. | D7, D8, D9, D10, D11, D12 | 6
 | 0402 | 0402 capacitor | C1_FLASH1, C1_FLASH2, C1_FLASH3, C2, C3, C4, C37, C44, C46, C47, C48 | 11 | Yageo (https://octopart-clicks.com/click/altium?sku=311-0.0JRCT-ND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) | RC0402JR-070RL (https://octopart-clicks.com/click/altium?sku=311-0.0JRCT-ND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) | Manual Solution | Digi-Key | 311-0.0JRCT-ND (https://octopart-clicks.com/click/altium?sku=311-0.0JRCT-ND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) | 0.01987 | 0.21857
 | 0402 | 0402 capacitor | C38 | 1 | KEMET (https://octopart-clicks.com/click/altium?sku=399-17558-1-ND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) | C0402C470J3RACAUTO (https://octopart-clicks.com/click/altium?sku=399-17558-1-ND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) | Volume Production | Digi-Key | 399-17558-1-ND (https://octopart-clicks.com/click/altium?sku=399-17558-1-ND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) | 0.17224 | 0.17224
 | 0402 | 0402 capacitor | C49, C50 | 2 | KEMET (https://octopart-clicks.com/click/altium?sku=399-17554-1-ND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) | C0402C220K4RAC7867 (https://octopart-clicks.com/click/altium?sku=399-17554-1-ND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) | Unknown | Digi-Key | 399-17554-1-ND (https://octopart-clicks.com/click/altium?sku=399-17554-1-ND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) | 0.25173 | 0.50346
 | 0402 | 0402 resistor | R1_FLASH1, R1_FLASH2, R1_FLASH3, R2, R3, R4, R5, R7, R8, R10, R28, R29, R65 | 13 | Panasonic (https://octopart-clicks.com/click/altium?sku=P10.0KLCT-ND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) | ERJ-2RKF1002X (https://octopart-clicks.com/click/altium?sku=P10.0KLCT-ND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) | Manual Solution | Digi-Key | P10.0KLCT-ND (https://octopart-clicks.com/click/altium?sku=P10.0KLCT-ND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) | 0.05962 | 0.77506
 | 0402 | 0402 resistor | R26, R27, R50, R51, R52 | 5 | Panasonic (https://octopart-clicks.com/click/altium?sku=P100LCT-ND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) | ERJ-2RKF1000X (https://octopart-clicks.com/click/altium?sku=P100LCT-ND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) | Manual Solution | Digi-Key | P100LCT-ND (https://octopart-clicks.com/click/altium?sku=P100LCT-ND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) | 0.05962 | 0.5962
 | 0402 | 0402 resistor | R49, R53 | 2 | Vishay (https://octopart-clicks.com/click/altium?sku=541-60.4LCT-ND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) | CRCW040260R4FKED (https://octopart-clicks.com/click/altium?sku=541-60.4LCT-ND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) | Volume Production | Digi-Key | 541-60.4LCT-ND (https://octopart-clicks.com/click/altium?sku=541-60.4LCT-ND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) | 0.13249 | 0.26498
 | 0402 | 0402 resistor | R54, R55 | 2 | Panasonic (https://octopart-clicks.com/click/altium?sku=P0.0JCT-ND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) | ERJ-2GE0R00X (https://octopart-clicks.com/click/altium?sku=P0.0JCT-ND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) | Volume Production | Digi-Key | P0.0JCT-ND (https://octopart-clicks.com/click/altium?sku=P0.0JCT-ND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) | 0.13249 | 0.26498
 | 0402 | 0402 resistor | R6, R9 | 2 | Panasonic (https://octopart-clicks.com/click/altium?sku=P4.7KDCCT-ND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) | ERA-2AEB472X (https://octopart-clicks.com/click/altium?sku=P4.7KDCCT-ND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) | Volume Production | Digi-Key | P4.7KDCCT-ND (https://octopart-clicks.com/click/altium?sku=P4.7KDCCT-ND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) | 0.5962 | 1.19
 | 0402 | 0402 resistor | R66, R67, R68, R69, R70, R71 | 6 | TE Connectivity (https://octopart-clicks.com/click/altium?sku=A129621CT-ND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) | CRGCQ0402F330R (https://octopart-clicks.com/click/altium?sku=A129621CT-ND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) | Unknown | Digi-Key | A129621CT-ND (https://octopart-clicks.com/click/altium?sku=A129621CT-ND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) | 0.02915 | 0.29148
 | 0402 | 0402 resistor | R72 | 1 | Yageo (https://octopart-clicks.com/click/altium?sku=YAG3474CT-ND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) | AC0402FR-0730KL (https://octopart-clicks.com/click/altium?sku=YAG3474CT-ND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) | Volume Production | Digi-Key | YAG3474CT-ND (https://octopart-clicks.com/click/altium?sku=YAG3474CT-ND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) | 0.13249 | 0.13249
 | 0603 | Inductor | L3 | 1 | TDK (https://octopart-clicks.com/click/altium?sku=445-17067-1-ND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) | MLZ1608N100LTD25 (https://octopart-clicks.com/click/altium?sku=445-17067-1-ND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) | Volume Production | Digi-Key | 445-17067-1-ND (https://octopart-clicks.com/click/altium?sku=445-17067-1-ND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) | 0.29148 | 0.29148
 | 0805 | 0805 capacitor | C36, C45 | 2 | Murata (https://octopart-clicks.com/click/altium?sku=490-14361-1-ND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) | GCM21BR70J106KE22K (https://octopart-clicks.com/click/altium?sku=490-14361-1-ND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) | Volume Production | Digi-Key | 490-14361-1-ND (https://octopart-clicks.com/click/altium?sku=490-14361-1-ND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) | 0.55646 | 1.11
 | 8MHz Crystal | 8MHz Abracom 4-pin crystal. | Y2 | 1 | Abracon (https://octopart-clicks.com/click/altium?sku=535-13456-1-ND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) | ABM3B-8.000MHZ-10-D-1-G-T (https://octopart-clicks.com/click/altium?sku=535-13456-1-ND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) | Volume Production | Digi-Key | 535-13456-1-ND (https://octopart-clicks.com/click/altium?sku=535-13456-1-ND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) | 1.51 | 1.51
 | ATMEGA64M1 | Atmel 8-bit AVR microcontroller. | U18 | 1 | Microchip / Atmel (https://octopart-clicks.com/click/altium?manufacturer=Microchip%20%2F%20Atmel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) | ATMEGA64M1-AU (https://octopart-clicks.com/click/altium?manufacturer=Microchip%20%2F%20Atmel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) | Volume Production | Digi-Key | ATMEGA64M1-AU-ND (https://octopart-clicks.com/click/altium?manufacturer=Microchip%20%2F%20Atmel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) | 7.11 | 7.11
 | DS3234 | SPI bus RTC with integrated crystal and SRAM | U2 | 1 | Maxim (https://octopart-clicks.com/click/altium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) | DS3234SN#T&R (https://octopart-clicks.com/click/altium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) | Volume Production | Digi-Key | DS3234SN#T&RCT-ND (https://octopart-clicks.com/click/altium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) | 11.25 | 11.25
 | SC18IS600IPW/S8HP | SPI to I2C bridge. | U4 | 1 | NXP USA (https://octopart-clicks.com/click/altium?sku=568-13690-1-ND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) | SC18IS600IPW/S8HP (https://octopart-clicks.com/click/altium?sku=568-13690-1-ND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) | Unknown | Digi-Key | 568-13690-1-ND (https://octopart-clicks.com/click/altium?sku=568-13690-1-ND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) | 4.05 | 4.05
 | SLW-102-01-G-D | 4 pos 100mil pitch low profile header | J8 | 1 | Samtec (https://octopart-clicks.com/click/altium?sku=SAM1088-02-ND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) | SLW-102-01-G-D (https://octopart-clicks.com/click/altium?sku=SAM1088-02-ND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) | Volume Production | Digi-Key | SAM1088-02-ND (https://octopart-clicks.com/click/altium?sku=SAM1088-02-ND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) | 1.02 | 1.02
 | SLW-103-01-G-D | 6 pos 100mil pitch low profile header | J7 | 1 | Samtec (https://octopart-clicks.com/click/altium?sku=SAM1088-03-ND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) | SLW-103-01-G-D (https://octopart-clicks.com/click/altium?sku=SAM1088-03-ND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) | Volume Production | Digi-Key | SAM1088-03-ND (https://octopart-clicks.com/click/altium?sku=SAM1088-03-ND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)
 | SLW-115-01-G-S | 15 Position Receptacle Connector 0.100" (2.54mm) Through Hole Gold | J3 | 1 | Samtec (https://octopart-clicks.com/click/altium?sku=SAM1089-15-ND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) | SLW-115-01-G-S (https://octopart-clicks.com/click/altium?sku=SAM1089-15-ND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) | Volume Production | Digi-Key | SAM1089-15-ND (https://octopart-clicks.com/click/altium?sku=SAM1089-15-ND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)
 | SN65HVD233D | 3.3V CAN Transceiver with Standby Mode, Loop-back 8-SOIC -40 to 125 | U14 | 1 | Texas Instruments (https://octopart-clicks.com/click/altium?sku=296-14639-5-ND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) | SN65HVD233D (https://octopart-clicks.com/click/altium?sku=296-14639-5-ND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) | Volume Production | Digi-Key | 296-14639-5-ND (https://octopart-clicks.com/click/altium?sku=296-14639-5-ND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) | 4.15 | 4.15
 | SN74HC365PW | Hex non-inverting buffer with 3-state outputs | U17 | 1 | Texas Instruments (https://octopart-clicks.com/click/altium?sku=296-33932-5-ND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) | SN74HC365PW (https://octopart-clicks.com/click/altium?sku=296-33932-5-ND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) | Volume Production | Digi-Key | 296-33932-5-ND (https://octopart-clicks.com/click/altium?sku=296-33932-5-ND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) | 0.88768 | 0.88768
 | SN74LVC1G07 | Single element non-inverting open drain buffer | U3 | 1 | Texas Instruments (https://octopart-clicks.com/click/altium?sku=296-8486-1-ND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) | SN74LVC1G07DCKR (https://octopart-clicks.com/click/altium?sku=296-8486-1-ND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) | Volume Production | Digi-Key | 296-8486-1-ND (https://octopart-clicks.com/click/altium?sku=296-8486-1-ND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) | 0.43722 | 0.43722
 | SST26VF016B | 2.5V/3.0V 16 Mbit Serial Quad I/O (SQI) Flash Memory | U1_FLASH1, U1_FLASH2, U1_FLASH3 | 3 | Microchip (https://octopart-clicks.com/click/altium?manufacturer=Microchip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) | SST26VF016B-104I/SN (https://octopart-clicks.com/click/altium?manufacturer=Microchip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) | Volume Production | Digi-Key | SST26VF016B-104I/SN-ND (https://octopart-clicks.com/click/altium?manufacturer=Microchip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) | 1.58 | 4.73
 | SW-PB | Schematic symbol for a generic 2-pin pushbutton, OFF-mom. | S2 | 1 | ITT C&K (https://octopart-clicks.com/click/altium?sku=CKN10587CT-ND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) | PTS830GM140SMTRLFS (https://octopart-clicks.com/click/altium?sku=CKN10587CT-ND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) | Volume Production | Digi-Key | CKN10587CT-ND (https://octopart-clicks.com/click/altium?sku=CKN10587CT-ND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) | 0.6757 | 0.6757
 | DPDT | DPDT Switch, customized for the pinout of the JS202011AQN switch. | S1 | 1 | ITT C&K (https://octopart-clicks.com/click/altium?sku=611-JS202011AQN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) | JS202011AQN (https://octopart-clicks.com/click/altium?sku=611-JS202011AQN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) | Volume Production | Mouser | 611-JS202011AQN (https://octopart-clicks.com/click/altium?sku=611-JS202011AQN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) | 0.5962 | 0.5962
 | SLH-010-1.50-G-D-A | 0.50 mm Razor Beam™ LP Ultra Low Profile Socket Strip, alignment pin option | J4 | 1 |  |  |  | SLH-010-1.50-G-D-A | Samtec
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

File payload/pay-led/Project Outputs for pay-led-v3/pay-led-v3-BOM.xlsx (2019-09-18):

Line # | Name | Value | Description | Designator | Quantity | Manufacturer 1 | Manufacturer Part Number 1 | Manufacturer Lifecycle 1 | Supplier 1 | Supplier Part Number 1 | Supplier Unit Price 1 | Supplier Subtotal 1
 | 402 | 10000pF | 0402 capacitor | C3 | 1 | Murata | GCM155R71H103KA55D | Volume Production | Digi-Key | 490-4762-1-ND | 0.13249 | 0.52996
 | 402 | 330 | 0402 resistor | R1_LED11, R1_LED12, R1_LED21, R1_LED22, R1_LED31, R1_LED32, R1_LED41, R1_LED42, R1_LED51, R1_LED52, R1_LED61, R1_LED62, R1_LED71, R1_LED72, R1_LED81, R1_LED82, R16 | 17 | TE Connectivity | CRGCQ0402F330R | Unknown | Digi-Key | A129621CT-ND | 0.01192 | 1.19
 | 2A 0402 | 120 Ohm @ 100MHz | Inductor | L1 | 1 | Murata | BLM15PX121SZ1D | Unknown | Digi-Key | 490-16505-1-ND | 0.19873 | 0.79494
 | 805 | 10uF | 0805 capacitor | C2, C5 | 2 | Murata | GCM21BR70J106KE22K | Volume Production | Digi-Key | 490-14361-1-ND | 0.38422 | 3.84
 | 402 | 10K | 0402 resistor | R9 | 1 | Panasonic | ERJ-2RKF1002X | Volume Production | Digi-Key | P10.0KLCT-ND | 0.13249 | 0.52996
 | 402 | 2 | 0402 resistor | R17 | 1 | Yageo | AC0402FR-072RL | Volume Production | Digi-Key | YAG3472CT-ND | 0.03975 | 0.39747
 | 603 | 1uF | 0603 capacitor | C4 | 1 | KEMET | C0603C105K4RACAUTO | Unknown | Digi-Key | 399-17704-1-ND | 0.19873 | 0.79494
 | 402 | 1K5 | 0402 resistor | R20, R21 | 2
 | 402 | 0.1uF | 0402 capacitor | C1 | 1 | Taiyo Yuden | EMK105B7104KVHF | Volume Production | Digi-Key | 587-3807-1-ND | 0.13249 | 0.52996
 | 402 | 0 | 0402 resistor | R10, R11, R12, R13, R14, R15, R18, R19 | 8 | Panasonic | ERJ-2GE0R00X | Volume Production | Digi-Key | P0.0JCT-ND | 0.02862 | 0.91577
 | DF13A-4P-1.25H(51) |  | 4 pos DF13 right angle surface mount connector | J1 | 1 | Hirose | DF13A-4P-1.25H(51) | Volume Production | Digi-Key | H125779CT-ND | 1.31 | 5.25
 | LED0603 |  | Generic 0603 LED. Use ChipLED from Osram for generic ones. | D9 | 1 | Osram Opto | LTQ39G-Q1OO-25-1 | Volume Production | Digi-Key | 475-3442-1-ND | 0.5962 | 2.38
 | LOP47K |  | LED ORANGE CLEAR SMD BOTTOM ENTRY | D1_LED11, D1_LED12, D1_LED21, D1_LED22, D1_LED31, D1_LED32, D1_LED41, D1_LED42, D1_LED51, D1_LED52, D1_LED61, D1_LED62, D1_LED71, D1_LED72, D1_LED81, D1_LED82 | 16 | Osram Opto | LOP47K-K2M1-24 | Unknown | Digi-Key | 475-3758-1-ND | 0.21715 | 21.72
 | MCP23017-QFN |  |  | U1 | 1 | Microchip | MCP23017-E/ML | Volume Production | Digi-Key | MCP23017-E/ML-ND | 1.92 | 7.68

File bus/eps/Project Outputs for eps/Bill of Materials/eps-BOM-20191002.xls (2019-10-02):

Line # | Name | Description | Value | Quantity | Designator | Library Reference | Manufacturer 1 | Manufacturer Part Number 1 | Manufacturer Lifecycle 1 | Supplier 1 | Supplier Part Number 1 | Supplier Unit Price 1 | Supplier Subtotal 1
1 | ADA4891-1ARJZ-R7 | Rail-to-rail amplifier 125mA max | Value | 4 | U4, U5, U7, U8 | ADA4891-1ARJZ-R7 | Rochester Electronics | ADA4891-1ARJZ-R7 | Volume Production | Digi-Key | ADA4891-1ARJZ-R7CT-ND | 1.98 | 7.93
2 | Part Number: 1SS389 | No Description Available | Value | 1 | D14 | 1SS389 | Comchip | 1SS389-G | Volume Production | Digi-Key | 641-1784-1-ND | 0.29092 | 0.29092
3 | 402 | Capacitor | 10000pF | 1 | C68 | Cap | Murata | GCM155R71H103KA55D | Manual Solution | Digi-Key | 490-4762-1-ND | 0.13249 | 0.13249
4 | 402 | 0402 resistor | 750K | 1 | R81 | RES0402 | Yageo | RC0402FR-07750KL | Volume Production | Digi-Key | YAG3228DKR-ND | 0.13224 | 0.13224
5 | 402 | 0402 resistor | 562K | 1 | R32 | RES0402 | Panasonic | ERJ-2RKF5623X | Manual Solution | Digi-Key | P562KLCT-ND | 0.13249 | 0.13249
6 | 402 | 0402 resistor | 511 | 1 | R83 | RES0402 | Panasonic | ERJ-2RKF5110X | Manual Solution | Digi-Key | P511LCT-ND | 0.13249 | 0.13249
7 | 402 | 0402 capacitor | 470nF | 1 | C59 | CAP0402 | Murata | GRM155R61A474KE15D | Volume Production | Digi-Key | 490-3264-6-ND | 0.17191 | 0.17191
8 | 402 | 0402 resistor | 412K | 1 | R37 | RES0402 | Panasonic | ERJ-2RKF4123X | Manual Solution | Digi-Key | P412KLCT-ND | 0.13249 | 0.13249
9 | 402 | 0402 resistor | 330 | 8 | R1, R3, R80, R81, R82, R83, R84, R85 | RES0402 | Panasonic | ERJ-2RKF3300X | Manual Solution | Digi-Key | P330LCT-ND | 0.05962 | 0.5962
10 | 402 | 0402 capacitor | 220pF | 1 | C? | CAP0402 | Murata | GCM155R71H221KA37D | Volume Production | Digi-Key | 490-4912-6-ND | 0.13224 | 0.13224
11 | 402 | 0402 resistor | 220K | 1 | R39 | RES0402 | Panasonic | ERJPA2F2203X | Manual Solution | Digi-Key | P17238CT-ND | 0.30473 | 0.30473
12 | 402 | 0402 resistor | 180K | 1 | R34 | RES0402 | Panasonic | ERJ-2RKF1803X | Manual Solution | Digi-Key | P180KLCT-ND | 0.13249 | 0.13249
 | 402 | 0402 resistor | 162K | 1 | R42 | RES0402 | Panasonic | ERJ-2RKF1623X | Volume Production | Digi-Key | P162KLDKR-ND | 0.13224 | 0.13224
14 | 402 | 0402 capacitor | 150nF | 1 | C? | CAP0402 | TDK | CGA2B1X7R1A154M050BC | Volume Production | Digi-Key | 445-12236-1-ND | 0.19835 | 0.19835
15 | 402 | 0402 resistor | 105 | 1 | R82 | RES0402 | Panasonic | ERJ-2RKF1050X | Manual Solution | Digi-Key | P105LCT-ND | 0.13249 | 0.13249
16 | 402 | 0402 capacitor | 100pF | 1 | C? | CAP0402 | KEMET | C0402C101J5RACAUTO | Unknown | Digi-Key | 399-17545-1-ND | 0.14546 | 0.14546
17 | 603 | 0603 capacitor | 100pF | 1 | C57 | CAP0603 | Murata | GCM1885C1H101JA16D | Volume Production | Digi-Key | 490-4767-6-ND | 0.21158 | 0.21158
19 | 402 | 0402 capacitor | 100nF | 4 | C1, C19, C22, C60 | CAP0402 | Taiyo Yuden | EMK105B7104KVHF | Volume Production | Digi-Key | 587-3807-6-ND | 0.13224 | 0.52894
20 | 402 | 0402 resistor | 100 | 10 | R9, R10, R13, R14, R15, R? | RES0402 | Panasonic | ERJ-2RKF1000X | Manual Solution | Digi-Key | P100LCT-ND | 0.05962 | 0.5962
 | 402 | 0402 capacitor | 82pF | 1 | C24 | CAP0402 | Murata | GCM1555C1H820FA16D | Unknown | Digi-Key | 490-16436-6-ND | 0.17191 | 0.17191
22 | 402 | 0402 resistor | 69.8K | 1 | R43 | RES0402 | Panasonic | ERJ-2RKF6982X | Manual Solution | Digi-Key | P69.8KLCT-ND | 0.13249 | 0.13249
23 | 402 | 0402 resistor | 60.4 | 2 | R12, R16 | RES0402 | Vishay | CRCW040260R4FKED | Volume Production | Digi-Key | 541-60.4LCT-ND | 0.13224 | 0.26447
24 | 12A | Inductor 50Ohms @ 100MHz | 50Ohms @ 100MHz | 1 | L4 | Inductor | Murata | BLM31SN500SZ1L | Volume Production | Digi-Key | 490-13270-1-ND | 0.48927 | 0.48927
25 | 402 | 0402 resistor | 50K | 5 | R8, R84_DEP-, R84_DEP+, R84_PAY LOAD SWITCH, R84_RBF | RES0402 | Panasonic | ERJ-2RKF4992X | Manual Solution | Digi-Key | P49.9KLCT-ND | 0.05962 | 0.5962
27 | 402 | 0402 capacitor | 47pF | 1 | C9 | CAP0402 | KEMET | C0402C470J3RACAUTO | Volume Production | Digi-Key | 399-17558-1-ND | 0.17191 | 0.17191
28 | 402 | 0402 capacitor | 33nF | 1 | C62 | CAP0402 | Murata | GRM155R71H333KE14D | Volume Production | Digi-Key | 490-11984-6-ND | 0.13224 | 0.13224
29 | 402 | 0402 resistor | 30K | 1 | R11 | RES0402 | Yageo | AC0402FR-0730KL | Volume Production | Digi-Key | YAG3474CT-ND | 0.13224 | 0.13224
30 | 1206 | 1206 capacitor | 22uF | 15 | C10, C11, C12, C13, C14, C16, C17, C18, C20, C21, C26, C27, C28, C70, C71 | CAP1206 | Murata | GCM31CR71A226KE02L | Unknown | Digi-Key | 490-14439-1-ND | 0.9402 | 14.1
 | 402 | 0402 capacitor | 22pF | 2 | C5, C6 | CAP0402 | KEMET | C0402C220K4RAC7867 | Unknown | Digi-Key | 399-17554-6-ND | 0.25125 | 0.5025
31 | 603 | 0603 capacitor | 22pF | 2 | C34, C35 | CAP0603 | KEMET | C0603C220K5RACAUTO | Manual Solution | Digi-Key | 399-13715-1-ND | 0.39747 | 0.79494
 | 402 | 0402 resistor | 15.8K | 1 | R41 | RES0402 | Panasonic | ERA-2AEB1582X | Volume Production | Digi-Key | P15.8KDCDKR-ND | 0.59506 | 0.59506
33 | 603 | Inductor | 10uH | 1 | L1 | Inductor | TDK | MLZ1608N100LTD25 | Volume Production | Digi-Key | 445-17067-6-ND | 0.29092 | 0.29092
34 | 805 | 0805 capacitor | 10uF 1-1.5 ESR | 1 | C? | CAP0805 | Murata | GCM21BR70J106KE22K | Volume Production | Digi-Key | 490-14361-1-ND | 0.73443 | 0.73443
35 | 805 | 0805 capacitor | 10uF | 13 | C1, C7, C8, C9, C41, C64_DEP-, C64_DEP+, C64_PAY LOAD SWITCH, C64_RBF, C67, C72, C? | CAP0805 | Murata | GCM21BR70J106KE22K | Volume Production | Digi-Key | 490-14361-1-ND | 0.5071 | 6.59
36 | 805 | 0805 resistor | 10mOhm | 8 | R15, R16, R17, R18, R30, R31, R36, R38 | RES0805 | Rohm | PMR10EZPFU8L00 | Volume Production | Digi-Key | RHM.008AJCT-ND | 0.85953 | 6.88
37 | 402 | 0402 resistor | 10K 1% | 5 | R56, R57, R58, R59, R60 | RES0402 | Vishay | CRCW0402-10K0FKED | Manual Solution | Digi-Key | 541-10.0KLCT-ND | 0.05035 | 0.50346
38 | 402 | 0402 thermistor | 10K 0.5% | 3 | R61, R62, R63 | RES0402 | Murata | NCP15XH103D03RC | Volume Production | Digi-Key | 490-12810-1-ND | 0.7273 | 2.18
39 | 402 | 0402 resistor | 10K | 21 | R2, R6, R7, R11, R12, R13, R14, R33, R35, R40, R44, R47, R48, R67, R68, R79, R84, R85, R? | RES0402 | Vishay | CRCW0402-10K0FKED | Manual Solution | Digi-Key | 541-10.0KLCT-ND | 0.05035 | 1.06
 | 402 | 0402 capacitor | 8.2nF | 1 | C25 | CAP0402 | Samsung | CL05B822KB5VPNC | New Product | Digi-Key | 1276-6570-1-ND | 0.13224 | 0.13224
41 | 402 | 0402 capacitor | 4.3nF | 1 | C61 | CAP0402 | Murata | GRM1557U1A432JA01D | Volume Production | Digi-Key | 490-8245-6-ND | 0.23802 | 0.23802
 | 402 | 0402 resistor | 2.7K | 1 | R4 | RES0402 | Panasonic | ERA-2AED272X | Volume Production | Digi-Key | P2.7KDECT-ND | 0.29092 | 0.29092
43 | IND_XAL6030-222MEB | Inductor | 2.2uH | 1 | L2 | IND_XAL6030-222MEB | Coilcraft | XAL6030-222MEB | Volume Production | Mouser | 994-XAL6030-222MEB | 2.45 | 2.45
44 | 402 | 0402 capacitor | 2.2nF | 1 | C58 | CAP0402 | Murata | GCM155R71H222KA37D | Volume Production | Digi-Key | 490-4914-6-ND | 0.13224 | 0.13224
45 | 402 | 0402 resistor | 2.2K | 2 | R45, R46 | RES0402 | Vishay | CRCW04022K20FKED | Manual Solution | Digi-Key | 541-2.20KLCT-ND | 0.13249 | 0.26498
 | 603 | 0603 capacitor | 2.2µF | 1 | C23 | CAP0603 | TDK | CGA3E1X7S1C225K080AC | Volume Production | Digi-Key | 445-16104-6-ND | 0.39671 | 0.39671
47 | 805 | 0805 resistor | 2mOhm | 1 | R5 | RES0805 | Panasonic | ERJ-8BWJR010V | Volume Production | Digi-Key | P.010AVCT-ND | 1.19 | 1.19
48 | 402 | Resistor | 2 | 1 | R86 | Res1 | Yageo | AC0402FR-072RL | Manual Solution | Digi-Key | YAG3472CT-ND | 0.13249 | 0.13249
 | 402 | 0402 capacitor | 1.8nF | 1 | C29 | CAP0402 | Murata | GCM155R71H182KA37D | Unknown | Digi-Key | 490-14429-6-ND | 0.13224 | 0.13224
50 | 603 | 0603 capacitor | 1uF | 12 | C63_DEP-, C63_DEP+, C63_PAY LOAD SWITCH, C63_RBF, C65_DEP-, C65_DEP+, C65_PAY LOAD SWITCH, C65_RBF, C? | CAP0603 | Samsung | CL10B105MO8NNWC | Volume Production | Digi-Key | 1276-6524-6-ND | 0.05554 | 0.66647
51 | 603 | Capacitor | 1uF | 1 | C69 | Cap | KEMET | C0603C105K4RACAUTO | Manual Solution | Digi-Key | 399-17704-1-ND | 0.19873 | 0.19873
52 | 402 | 0402 resistor | 1M | 1 | R80 | RES0402 | Vishay Beyschlag | MCS04020C1004FE000 | Volume Production | Digi-Key | MCS0402-1.00M-CFDKR-ND | 0.39671 | 0.39671
53 | 402 | 0402 resistor | 1K | 5 | R?, R?_HEATER CONTROL 1, R?_HEATER CONTROL 2 | RES0402 | Panasonic | ERJ-PA2J102X | Volume Production | Digi-Key | P17193CT-ND | 0.21158 | 1.06
54 | 402 | 0402 capacitor | 0.1uF | 21 | C2, C3, C4, C8, C15, C30, C31, C45, C46_IMON_3V3, C46_IMON_5V, C46_PACK_IMON, C46_X- IMON, C46_X+ IMON, C46_Y- IMON, C46_Y+ IMON, C56, C?, C?_HEATER CONTROL 1, C?_HEATER CONTROL 2 | CAP0402 | Taiyo Yuden | EMK105B7104KVHF | Manual Solution | Digi-Key | 587-3807-1-ND | 0.06889 | 1.45
55 | 402 | 0402 capacitor | 0.1pF | 2 | C32, C33 | CAP0402 | Murata | GCQ1555C1HR10BB01D | Manual Solution | Digi-Key | 490-17533-1-ND | 0.47696 | 0.95393
56 | 603 | 0603 capacitor | 0.01uF | 1 | C56 | CAP0603 | Murata | GRM188R70J103KA01D | Volume Production | Digi-Key | 490-9729-1-ND | 0.13224 | 0.13224
57 | 402 | 0402 resistor | 0 | 8 | R17, R18, R69, R70, R71, R72, R73, R74 | RES0402 | Panasonic | ERJ-2GE0R00X | Volume Production | Digi-Key | P0.0JCT-ND | 0.03967 | 0.39671
58 | ABS07-120-32.768KHZ-T | 3.2 x 1.5mm, 32.768KHZ Xtal 6pf, 20ppm, -40+85C, ESR 60kOhm, ST Micro Ref Design Crystal for STM32L |  | 1 | Y1 | ABS07-120-32.768KHZ-T | Abracon | ABS07-120-32.768KHZ-T | Volume Production | Digi-Key | 535-11937-1-ND | 0.75374 | 0.75374
59 | SN65HVD233D | 3.3V CAN Transceiver with Standby Mode, Loop-back 8-SOIC -40 to 125 |  | 1 | U2 | SN65HVD233D | Texas Instruments | SN65HVD233D | Volume Production | Digi-Key | 296-14639-5-ND | 4.14 | 4.14
60 | SN74LV1T34DBVR | Single Power Supply BUFFER Logic Level Shifter _no enable_ 5-SOT-23 -40 to 125 |  | 2 | U1, U2 | SN74LV1T34DBVR | Texas Instruments | SN74LV1T34DBVR | Volume Production | Digi-Key | 296-37176-1-ND | 0.62151 | 1.24
61 | TPS22959DNYT | 5.5V, 15A, 4.4mÎ© Load Switch with Quick Output Discharge 8-WSON -40 to 85 |  | 4 | U22_DEP-, U22_DEP+, U22_PAY LOAD SWITCH, U22_RBF | TPS22959DNYT | Texas Instruments | TPS22959DNYT | Not Recommended for New Design | Digi-Key | 296-47872-1-ND | 2.53 | 10.1
62 |  | Just a generic LED |  | 1 | D1 | LED
63 | 8MHz Crystal | 8MHz Abracom 4-pin crystal. |  | 1 | Y1 | AMB3B-8MHz | Abracon | ABM3B-8.000MHZ-10-D-1-G-T | Volume Production | Digi-Key | 535-13456-1-ND | 1.51 | 1.51
64 | 3084 | CR2330 Battery Holder |  | 1 | RTC_BATT | 3084 | Keystone Electronics | 3084 | Volume Production | Digi-Key | 36-3084-ND | 0.81986 | 0.81986
65 | 504050-0691 | Wire-To-Board Connector, Pico-Lock 504050 Series, Surface Mount, Header, 6, 1.5 mm |  | 1 | J3 | 504050-0691 | Molex | 5040500691 | Volume Production | Digi-Key | WM10143CT-ND | 1.9 | 1.9
66 | 836149012 | Mini-DSUB 25-pos Connector |  | 1 | J1 | 836149012 | Molex | 836149012 | End of Life | Digi-Key | WM2144-ND | 25.75 | 25.75
67 | AD8613 | Low power, low noise rail-to-rail op-amp. |  | 1 | U? | AD8613 | Rochester Electronics | AD8613AKSZ-REEL7 | Unknown | Digi-Key | AD8613AKSZ-REEL7CT-ND | 1.81 | 1.81
68 | ADS7953 | 12 bit, 16 channel ADC |  | 1 | U? | ADS7953 | Texas Instruments | ADS7953SBRHBT | Volume Production | Digi-Key | 296-25844-1-ND | 14.6 | 14.6
69 | AP9101C-COTRG | Battery Protection IC |  | 1 | *1 | AP9101C-COTRG
70 | ATMEGA64M1 | Atmel 8-bit AVR microcontroller. |  | 1 | U1 | ATMEGA64M1_QFP | Microchip | ATMEGA64M1-AU | Unknown | Digi-Key | ATMEGA64M1-AU-ND | 7.1 | 7.1
71 | CSD16406Q3 | Power MOSFET |  | 4 | Q1, Q2, Q3, Q4 | CSD16406Q3 | Texas Instruments | CSD16406Q3 | Volume Production | Digi-Key | 296-24251-1-ND | 1.45 | 5.82
72 | DAC7562 | 12-bit, low-power, voltage-output DAC with internal reference. |  | 1 | U? | DAC7562 | Texas Instruments | DAC7562SDGSR | Volume Production | Digi-Key | 296-29022-1-ND | 7.93 | 7.93
73 | DF13A-2P-1.25H(21) | 2 pos DF13 right angle surface mount connector |  | 7 | DEP-, DEP+, HEAT1, HEAT2, J6, THM1, THM2 | DF13A-2P-1.25H(21) | Hirose | DF13A-2P-1.25H(21) | Volume Production | Digi-Key | H125743CT-ND | 0.56861 | 3.98
74 | DF13A-4P-1.25H(51) | 4 pos DF13 right angle surface mount connector |  | 4 | PX-, PX+, PY-, PY+ | DF13A-4P-1.25H(51) | Hirose | DF13A-4P-1.25H(51) | Volume Production | Digi-Key | H125779CT-ND | 1.31 | 5.24
75 | DF13A-15P-1.25H(21) | 15 pos DF13 right angle surface mount connector |  | 1 | J4 | DF13A-15P-1.25H(21) | Hirose | DF13A-15P-1.25H(21) | Volume Production | Digi-Key | H125988CT-ND | 1.6 | 1.6
76 | DPDT | DPDT Switch, customized for the pinout of the JS202011AQN switch. |  | 1 | S1 | DPDT Switch | ITT C&K | JS202011AQN | Volume Production | Digi-Key | 401-2000-ND | 0.56861 | 0.56861
77 | eFuse | 2.7 - 24 V input supply, 15 A max load current |  | 1 | U21 | TPS25982 | Texas Instruments | TPS259822LNRGER | Unknown | Digi-Key | 296-53584-1-ND | 5.24 | 5.24
78 | ESDA7P60-1U1M | Diode |  | 1 | D13 | ESDA7P60-1U1M | STMicroelectronics | ESDA7P60-1U1M | Volume Production | Digi-Key | 497-16253-1-ND | 0.59506 | 0.59506
79 | ESQ-126-23-G-D | PC/104(TM) Elevated Socket Strip, Through-hole, Vertical, -55 to 125 degC, 2.54 mm Pitch, 52-Pin, Female, RoHS |  | 1 | H1 | ESQ-126-23-G-D | Samtec | ESQ-126-23-G-D | Volume Production | Newark | 92P1348 | 18.43 | 18.43
80 | ESQ-126-23-G-D | PC/104(TM) Elevated Socket Strip, Through-hole, Vertical, -55 to 125 degC, 2.54 mm Pitch, 52-Pin, Female, RoHS |  | 1 | H2 | ESQ-126-23-G-D | Samtec | ESQ-126-23-G-D | Volume Production | Newark | 92P1348 | 18.43 | 18.43
81 | Header 2 | Header, 2-Pin |  | 1 | P1 | Header 2 | Wurth Electronics | 61300211121 | Volume Production | Digi-Key | 732-5315-ND | 0.17191 | 0.17191
82 | IMU BNO080 | ACCEL/GYRO/MAG I2C 32BIT |  | 1 | U13 | IMU BNO080 | Hillcrest Laboratories | BNO080 | Unknown | Digi-Key | 1888-1000-1-ND | 17.83 | 17.83
83 | INA214CQDCKRQ1 | IC CURR SENSE 1 CIRCUIT SC70-6 |  | 7 | U8_IMON_3V3, U8_IMON_5V, U8_PACK_IMON, U8_X- IMON, U8_X+ IMON, U8_Y- IMON, U8_Y+ IMON | INA214CQDCKRQ1 | Texas Instruments | INA214CQDCKRQ1 | Unknown | Digi-Key | 296-51151-1-ND | 2.26 | 15.83
84 | IND_XAL4020-102ME | 1uH 20% 9.6A 14.60mOhms AEC-Q200 |  | 1 | L1 | IND_XAL4020-102ME | Coilcraft | XAL4020-102MEC | Volume Production | Mouser | 994-XAL4020-102MEC | 2.38 | 2.38
85 | IPBT-102-H1-T-S-RA-K | Samtec Connector Through Hole, Right Angle 2 pos 0.165" (4.20mm) pitch |  | 1 | J5 | IPBT-102-H1-T-S-RA-K | Samtec | IPBT-102-H1-T-S-RA-K | Not Recommended for New Design | Digi-Key | SAM9552-ND | 1.84 | 1.84
86 | IRL6297SDPbF |  |  | 1 | U6 | IRL6297SDPbF | International Rectifier | IRL6297SDTRPBF | Volume Production | Digi-Key | IRL6297SDTRPBF-ND
87 | LED0603 | Generic 0603 LED. Use ChipLED from Osram for generic ones. |  | 8 | D2, D3, D4, D5, D6, D7, D?_HEATER CONTROL 1, D?_HEATER CONTROL 2 | LED0603
88 | MCP23S17-QFN | 16 channel SPI port expander |  | 1 | U6 | MCP23S17-QFN | Microchip | MCP23S17T-E/ML | Volume Production | Digi-Key | MCP23S17T-E/MLCT-ND | 2.06 | 2.06
89 | MCP6546 | Open-drain output sub-microamp comparator. |  | 2 | U?_HEATER CONTROL 1, U?_HEATER CONTROL 2 | MCP6546 | Microchip | MCP6546T-E/OT | Volume Production | Digi-Key | MCP6546T-E/OTCT-ND | 0.48927 | 0.97855
90 | N-MOS | 20V 6.2A, N-MOS, low gate on voltage |  | 2 | Q?_HEATER CONTROL 1, Q?_HEATER CONTROL 2 | FDC637BNZCT-ND | Rochester Electronics | FDC637BNZ | Volume Production | Digi-Key | FDC637BNZCT-ND
91 | REF5025 | Voltage Reference |  | 1 | U? | REF5025 | Texas Instruments | REF5025AIDGKR | Volume Production | Digi-Key | 296-41382-1-ND | 3.97 | 3.97
92 | SLW-102-01-G-D | 4 pos 100mil pitch low profile header |  | 1 | J4 | SLW-102-01-G-D | Samtec | SLW-102-01-G-D | Volume Production | Digi-Key | SAM1088-02-ND | 1.02 | 1.02
93 | SLW-103-01-G-D | 6 pos 100mil pitch low profile header |  | 3 | 3V3, 5V, J3 | SLW-103-01-G-D | Samtec | SLW-103-01-G-D | Volume Production | Digi-Key | SAM1088-03-ND
94 | SM74611 | PV Diode |  | 4 | D2, D3, D4, D5 | SM74611 | Texas Instruments | SM74611KTTR | Volume Production | Digi-Key | 296-35688-1-ND | 4.76 | 19.04
95 | SN74HC365PW | Hex non-inverting buffer with 3-state outputs |  | 1 | U11 | SN74HC365PW | Texas Instruments | SN74HC365PW | Volume Production | Digi-Key | 296-33932-5-ND | 0.88598 | 0.88598
96 | SW-PB | Schematic symbol for a generic 2-pin pushbutton, OFF-mom. |  | 1 | S2 | Pushbutton - Low Profile | ITT C&K | PTS830GM140SMTRLFS | Volume Production | Digi-Key | CKN10587CT-ND | 0.6744 | 0.6744
97 | TC7WB67CFKLF | Active high bus switch |  | 1 | U3 | TC7WB66CFKLF | Toshiba | TC7WB67CFK,LF(CT | Unknown | Digi-Key | TC7WB67CFKLF(CTCT-ND | 0.54217 | 0.54217
98 | TLH-010-0.50-G-D-A | 0.50 mm Razor Beam LP Ultra Low Profile Terminal Strip, alignment pin option |  | 1 | J2 | TLH-010-0.50-G-D-A |  |  |  | Samtec | TLH-010-0.50-G-D-A
99 | TPS61088 | Boost converter |  | 1 | U12 | TPS61088 | Texas Instruments | TPS61088RHLT | New Product | Digi-Key | 296-42129-1-ND | 5.84 | 5.84
100 | TPS630250 | Buck-boost converter |  | 1 | U11 | TPS630250 | Texas Instruments | TPS630250RNCT | Volume Production | Digi-Key | 296-42036-6-ND | 3.83 | 3.83

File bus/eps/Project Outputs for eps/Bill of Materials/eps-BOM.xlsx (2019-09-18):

Line # | Name | Description | Value | Designator | Quantity | Library Reference | Manufacturer 1 | Manufacturer Part Number 1 | Manufacturer Lifecycle 1 | Supplier 1 | Supplier Part Number 1 | Supplier Unit Price 1 | Supplier Subtotal 1 | Supplier 2 | Supplier Part Number 2 | Supplier Unit Price 2 | Supplier Subtotal 2 | Supplier 3 | Supplier Part Number 3 | Supplier Unit Price 3 | Supplier Subtotal 3 | Manufacturer 4 | Manufacturer Part Number 4 | Manufacturer Lifecycle 4 | Supplier 4 | Supplier Part Number 4 | Supplier Unit Price 4 | Supplier Subtotal 4 | Supplier 5 | Supplier Part Number 5 | Supplier Unit Price 5 | Supplier Subtotal 5 | Supplier 6 | Supplier Part Number 6 | Supplier Unit Price 6 | Supplier Subtotal 6 | Manufacturer 7 | Manufacturer Part Number 7 | Manufacturer Lifecycle 7 | Supplier 7 | Supplier Part Number 7 | Supplier Unit Price 7 | Supplier Subtotal 7 | Supplier 8 | Supplier Part Number 8 | Supplier Unit Price 8 | Supplier Subtotal 8 | Supplier 9 | Supplier Part Number 9 | Supplier Unit Price 9 | Supplier Subtotal 9
1 | ADA4891-1ARJZ-R7 | Rail-to-rail amplifier 125mA max | Value | U4, U5, U7, U8 | 4 | ADA4891-1ARJZ-R7 | Rochester Electronics | ADA4891-1ARJZ-R7 | Volume Production | Digi-Key | ADA4891-1ARJZ-R7CT-ND | 1.99 | 7.95
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

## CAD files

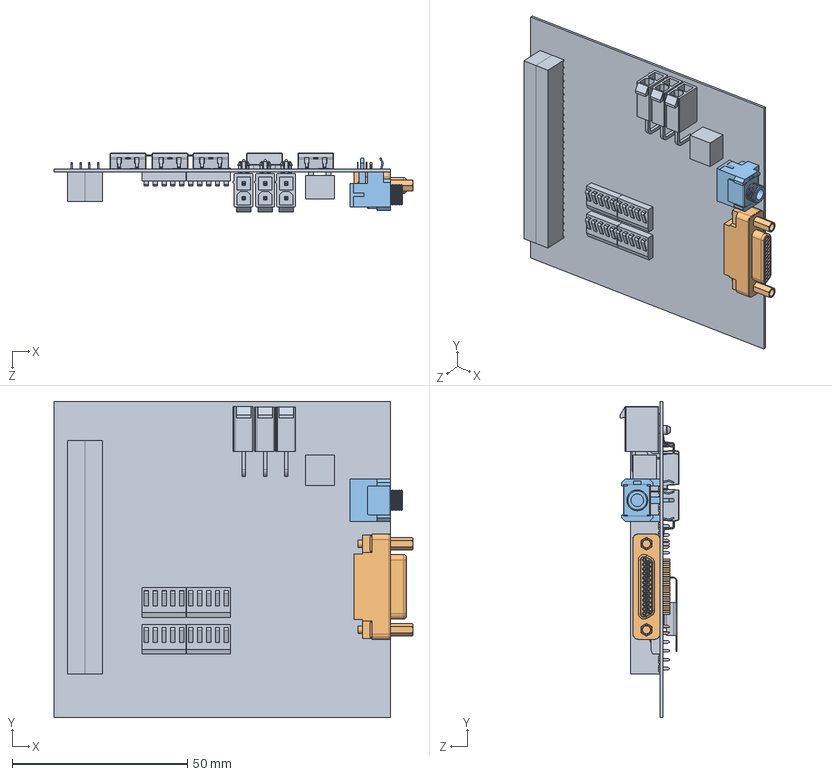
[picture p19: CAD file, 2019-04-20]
bus/eps/Project Outputs for eps/CAD Model/EPS.SLDASM
102.3 x 90.2 x 16.7 mm
eps_defeature
[MiniD] 836149012 v1.step
[RBF] CUI_SJ1-3544 v1.step

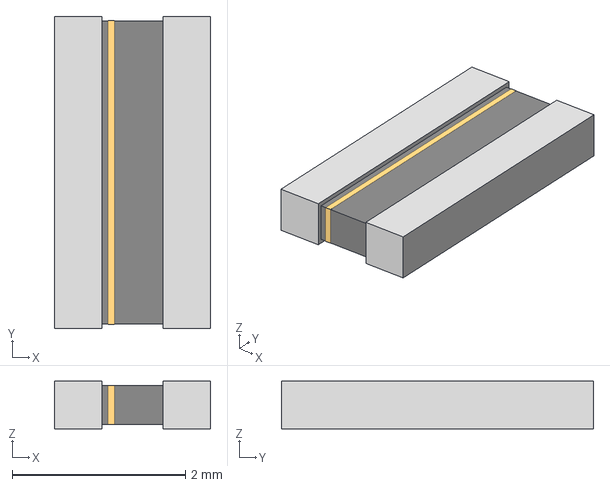
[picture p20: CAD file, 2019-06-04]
bus/eps-prototype-pcbs/motorRegulator/2019-06-03_23-23-21/STEP/RES_3216-M.step
1.80 x 3.60 x 0.55 mm

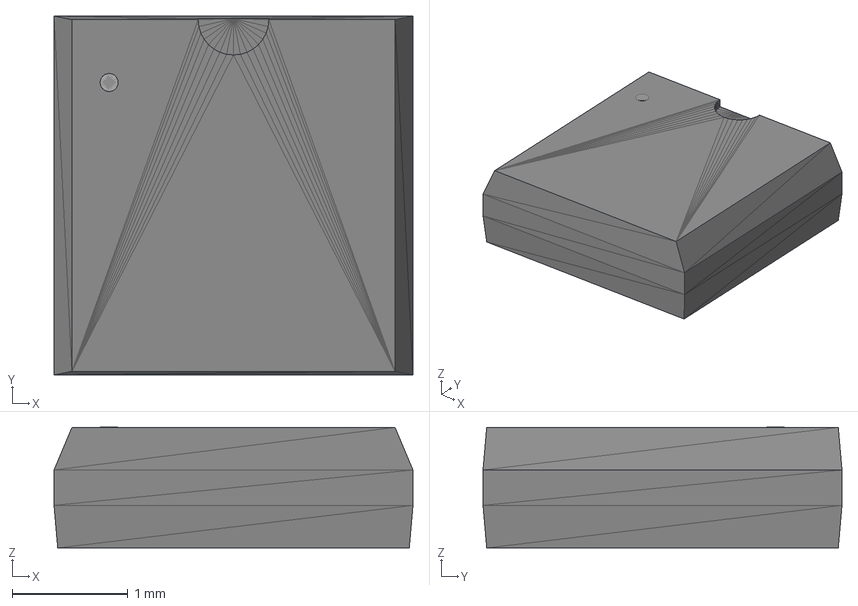
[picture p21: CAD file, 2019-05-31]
bus/eps-prototype-pcbs/motorRegulator/LM3478 Models/STEP/MUA08A.step
3.10 x 3.10 x 1.04 mm

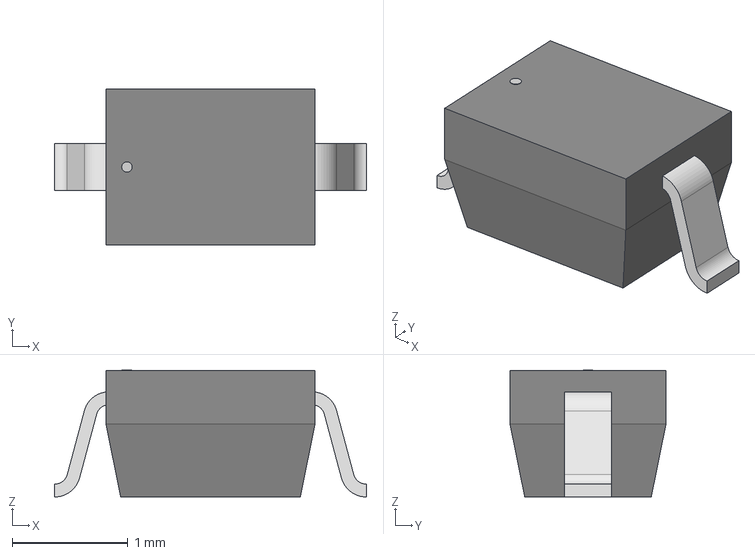
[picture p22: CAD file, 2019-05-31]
bus/eps-prototype-pcbs/motorRegulator/Schottky Diode Models/STEP/SOD323F-L.step
2.69 x 1.35 x 1.09 mm

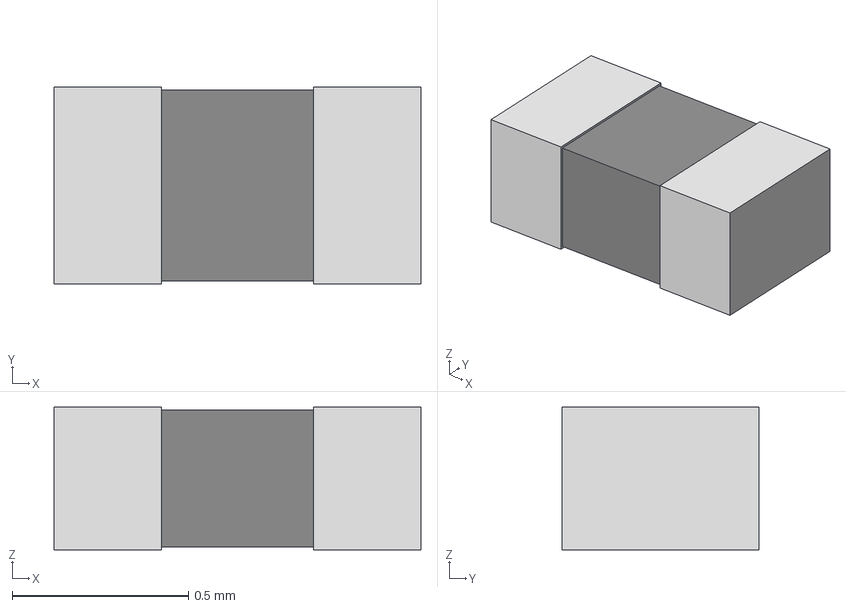
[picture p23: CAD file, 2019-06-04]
bus/eps-prototype-pcbs/motorRegulator/UL_CRCW040211K5FKED/STEP/RES_CRCW_0402-L.step
1.04 x 0.558 x 0.406 mm

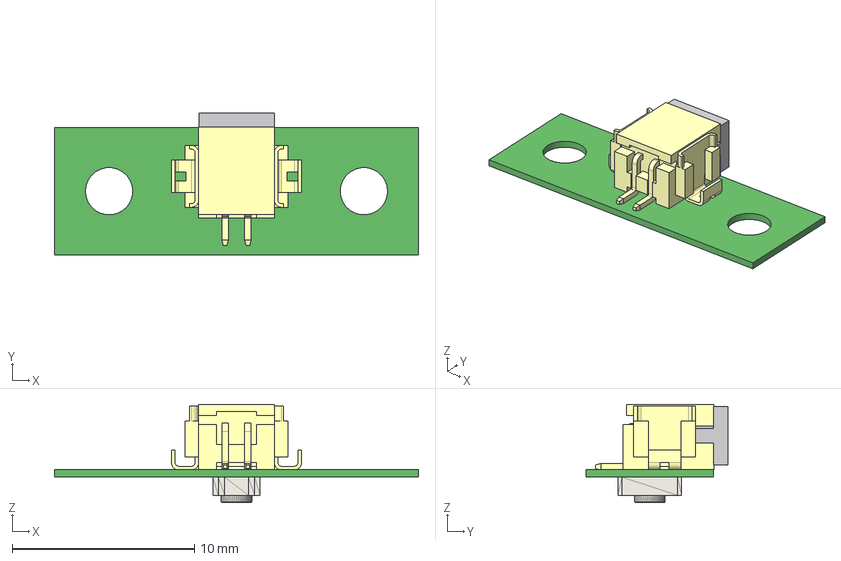
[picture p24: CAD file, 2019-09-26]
payload/pay-lim-switch/Project Outputs for pay-lim-switch/pay-lim-switch_2019-09-25.step
20.0 x 7.79 x 5.39 mm
Board
PTS830GM140_SMTR_LFS_-_Pushbutton_v2
\X\88\Ü3\X\92\X\85\X\83P\X\81[\X\83X
DF13A-2P-1.25H\X\8A\ÜH\X\97\Ü*

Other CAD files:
bus/eps-prototype-pcbs/motorRegulator/RES_3216.step
bus/eps-solar-panel-pcb/Project Outputs for SolarPanel/AutoCAD PCB/SolarPanel_v2.DWG
bus/eps-solar-panel-pcb/Project Outputs for SolarPanel_+X/AutoCAD PCB/SolarPanel_+X_v2.DWG
bus/eps-prototype-pcbs/motorRegulator/2019-06-03_23-23-21/STEP/RES_3216-L.step
bus/eps-prototype-pcbs/motorRegulator/LM3478 Models/STEP/MUA08A-M.step
bus/eps-prototype-pcbs/motorRegulator/Schottky Diode Models/STEP/SOD323F.step
bus/eps-prototype-pcbs/motorRegulator/UL_CRCW040211K5FKED/STEP/RES_CRCW_0402.step
bus/eps-prototype-pcbs/motorRegulator/LM3478 Models/STEP/MUA08A-L.step
bus/eps-prototype-pcbs/motorRegulator/Schottky Diode Models/STEP/SOD323F-M.step
bus/eps-prototype-pcbs/motorRegulator/UL_CRCW040211K5FKED/STEP/RES_CRCW_0402-M.step

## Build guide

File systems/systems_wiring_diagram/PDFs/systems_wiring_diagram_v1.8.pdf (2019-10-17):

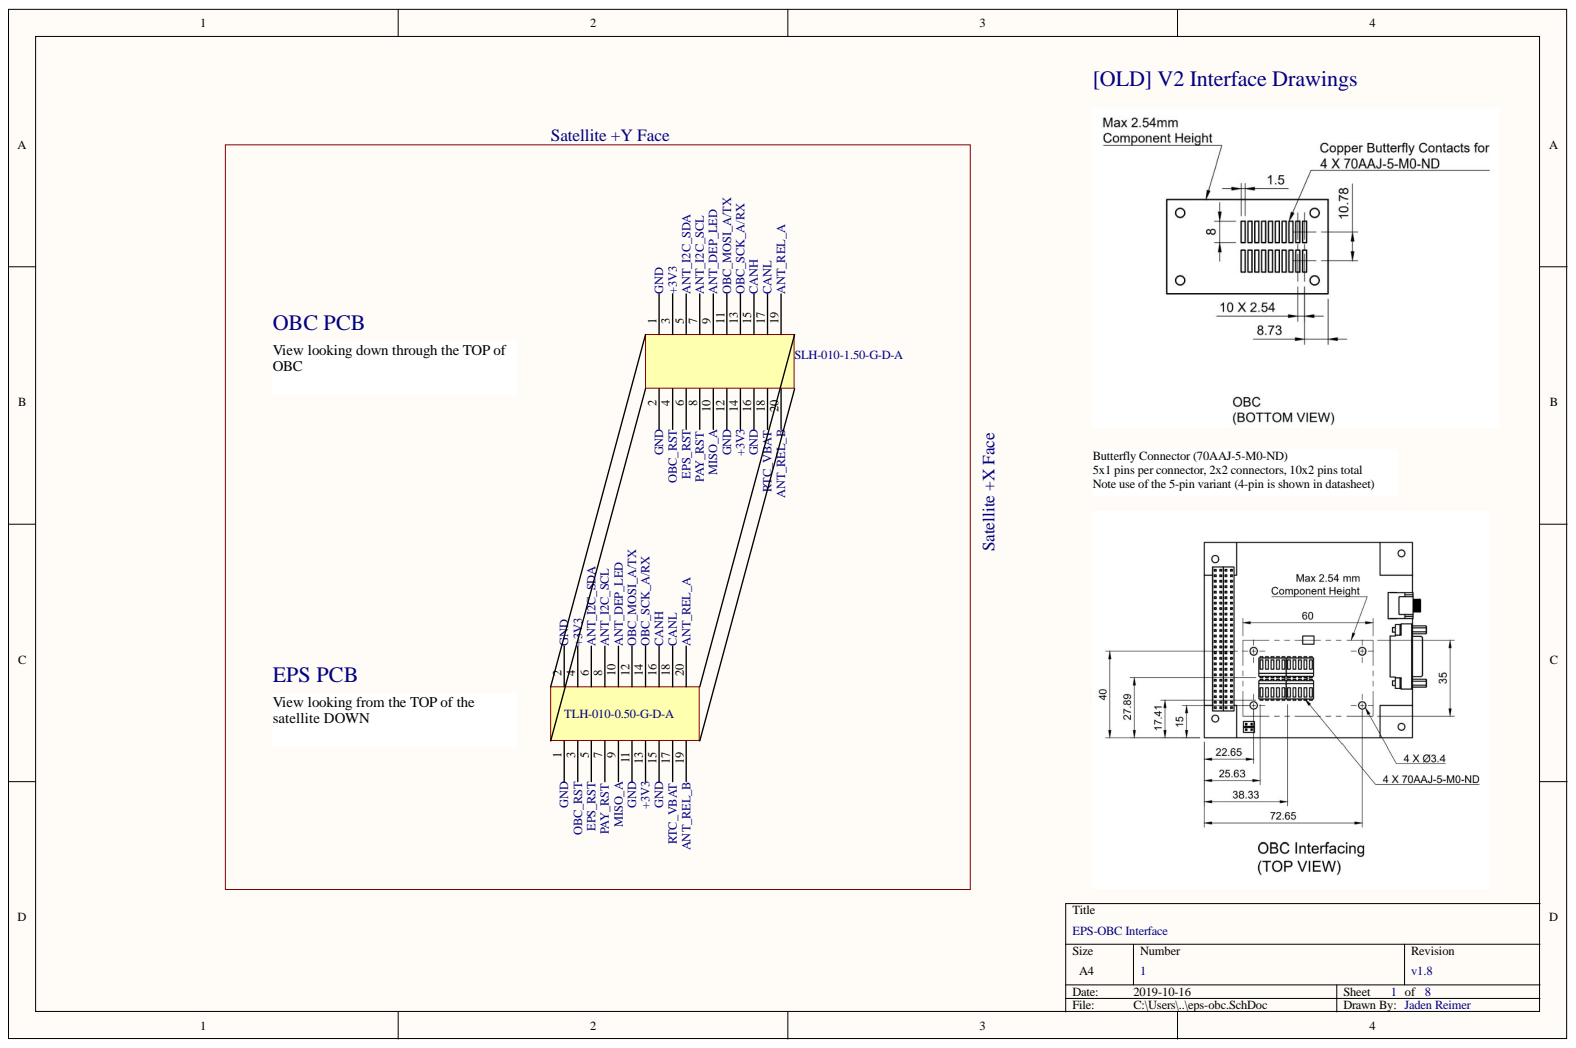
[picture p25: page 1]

View looking down through the TOP of
OBC

Butterfly Connector (70AAJ-5-M0-ND)
5x1 pins per connector, 2x2 connectors, 10x2 pins total
Note use of the 5-pin variant (4-pin is shown in datasheet)

View looking from the TOP of the
satellite DOWN

Size A4 | Number 1 | Revision v1.8

Date: 2019-10-16 | Sheet 1 of 8
File: C:\Users\..\eps-obc.SchDoc | Drawn By: Jaden Reimer

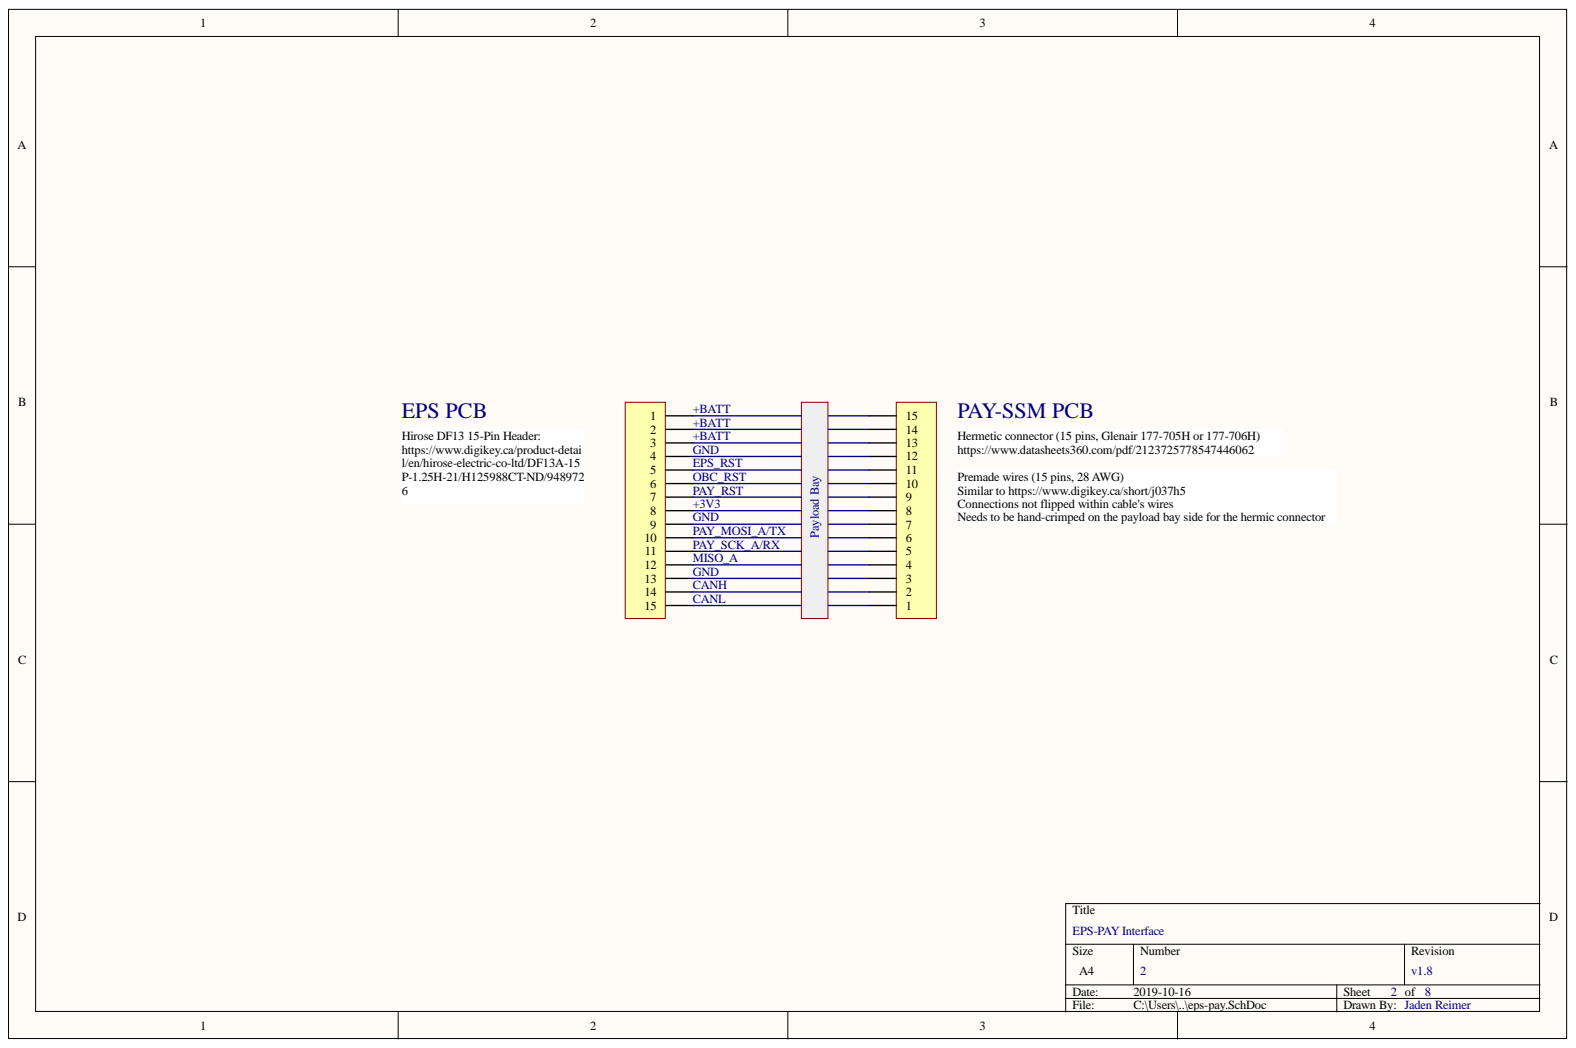
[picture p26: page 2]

(15 pins, 28
within
rimped on the payload bay side

eds to be hand-

Numbe r 2 | R evision v1. 8

: 2019-10-16 | She et 2 of 8
File : C:\Use rs\. .\eps-pa y . S chDoc | D r a wn By: Jaden R eime r

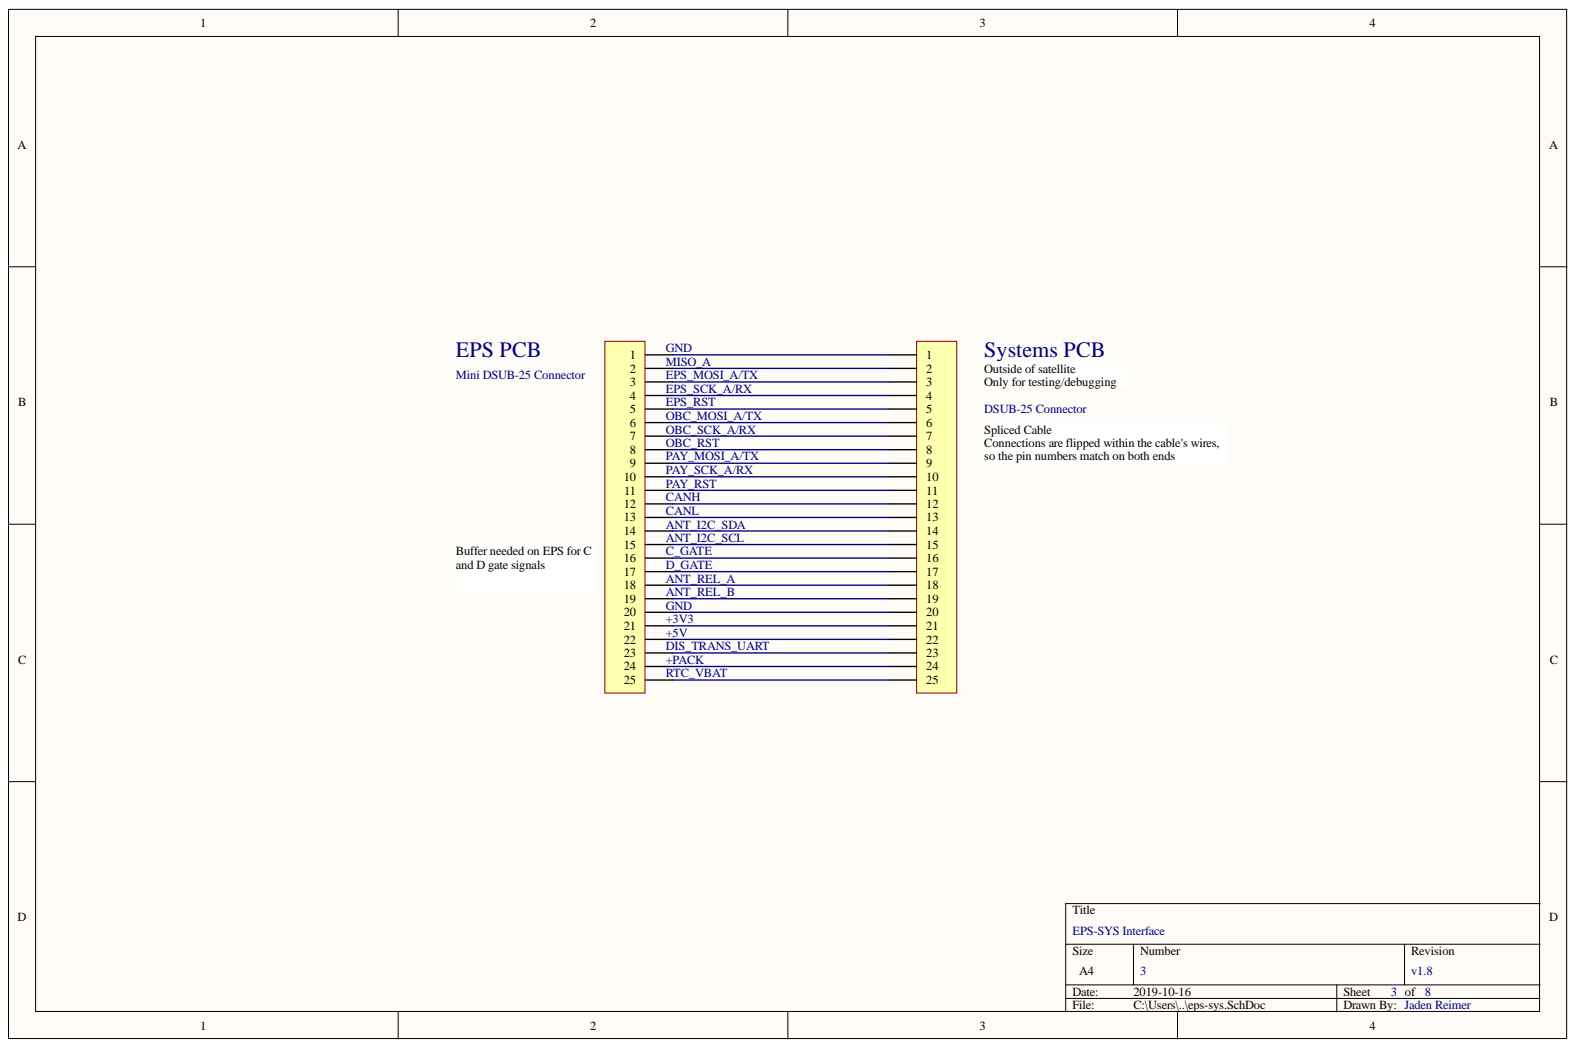
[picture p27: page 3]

Outside of satellite Only for testing/debugging

Numbe r 3 | R evision v1. 8

: 2019-10-16 | She et 3 of 8
File : C:\Use rs\. .\eps-sys. S chDoc | D r a wn By: Jaden R eime r

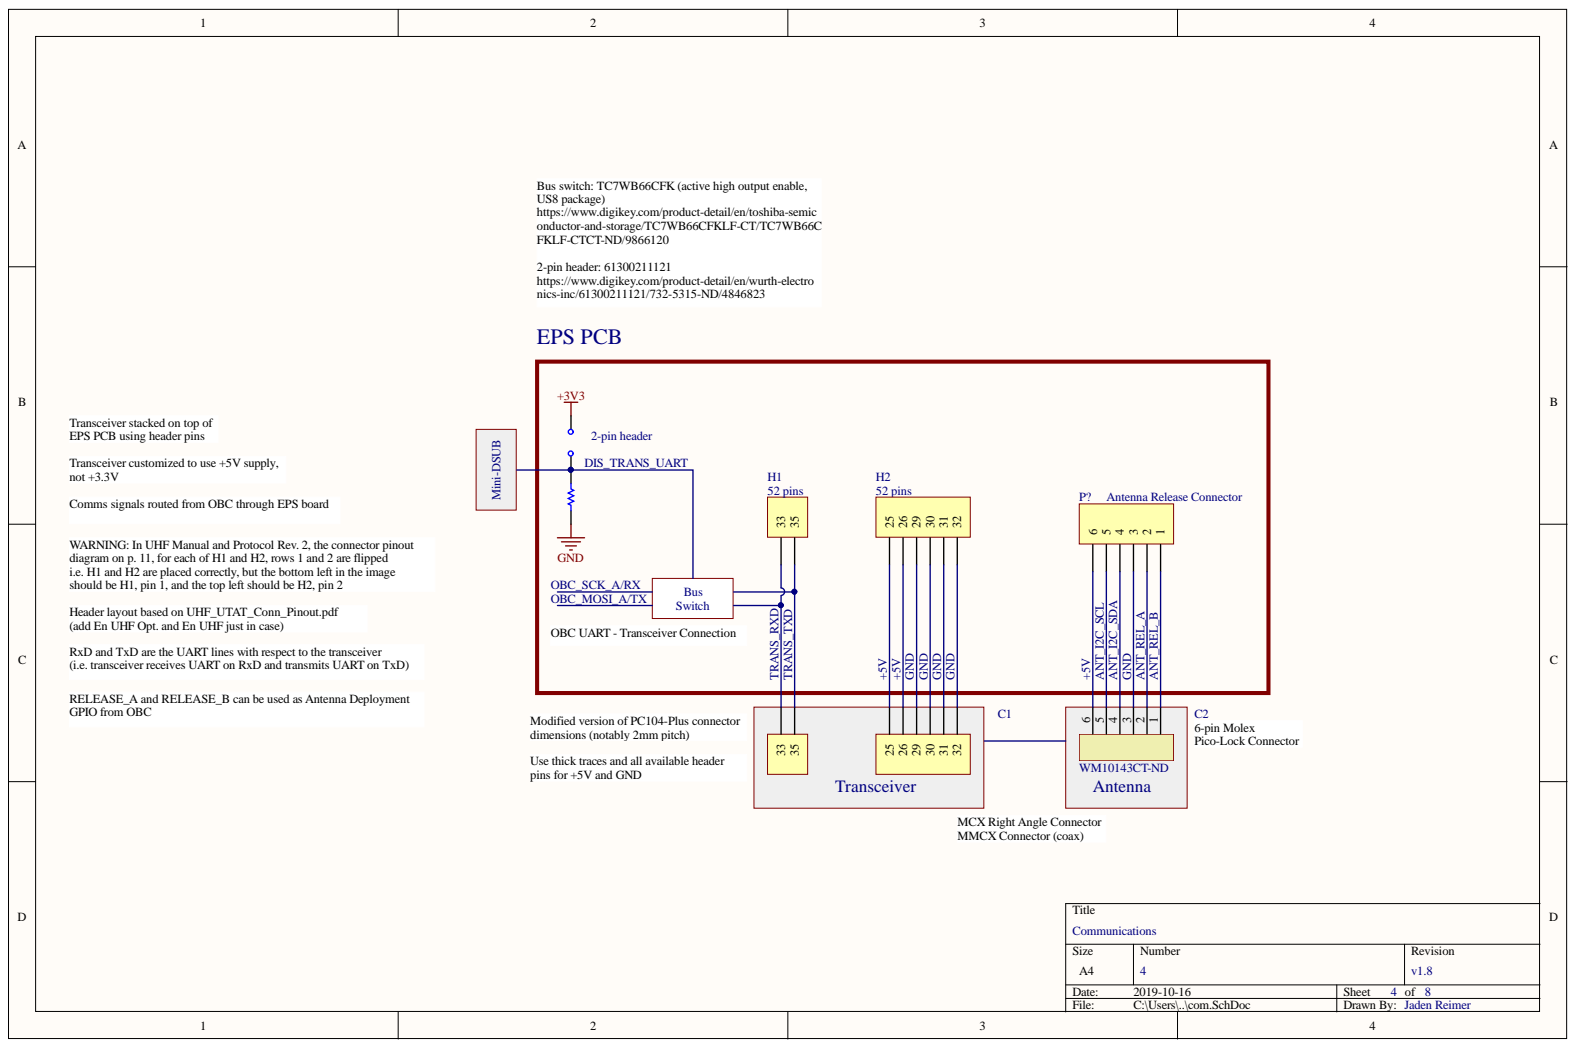
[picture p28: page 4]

com/product-detail/en/toshiba

com/product-detail/en/wurth-

+3V | 3 2-pin he ade r

cked on top of
ade

for
are pla
and the top le

S witc h

ct to the tr
and tr

6-pin Molex Pico-Lock Conne

Numbe r | R evision 8

: 2019-10-16 | She et 4 of 8
File : C:\Use rs\. .\com. S chDoc | D r a wn By: Jaden R eime r

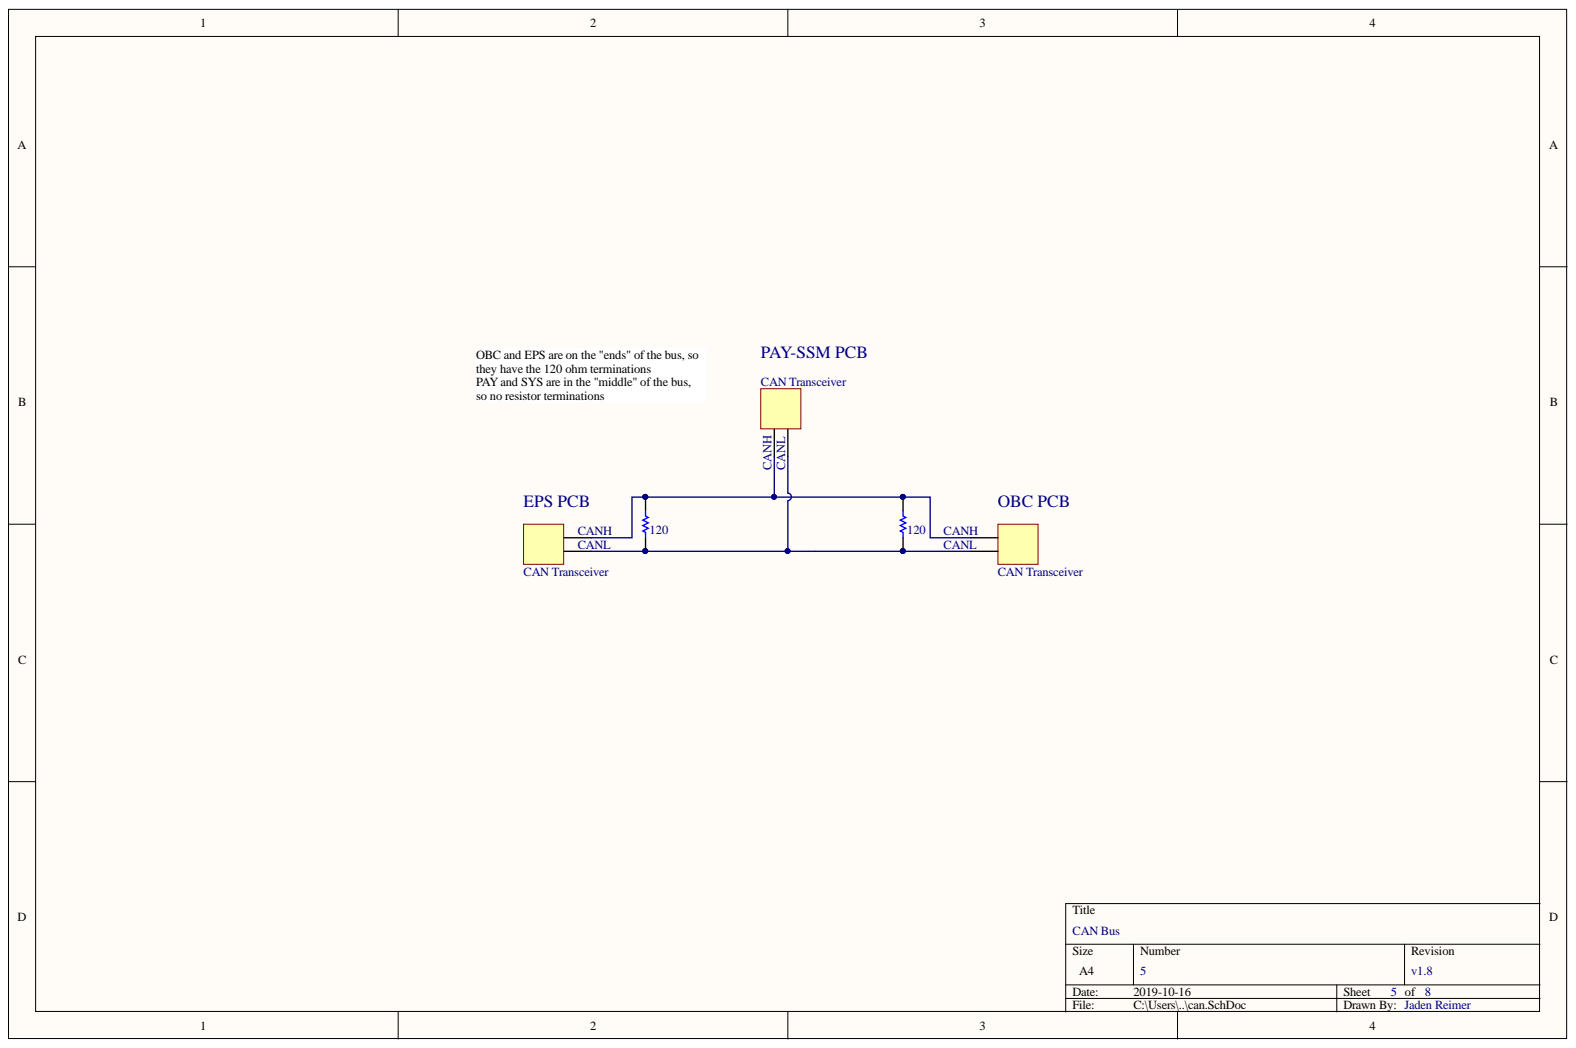
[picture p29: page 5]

PAY-SSM PCB they have the 120 ohm terminations PAY and SYS are in the "middle" of the bus,

ends" of the bus, so

Numbe r 5 | R evision v1. 8

: 2019-10-16 | She et 5 of 8
File : C:\Use rs\. .\c an. S chDoc | D r a wn By: Jaden R eime r

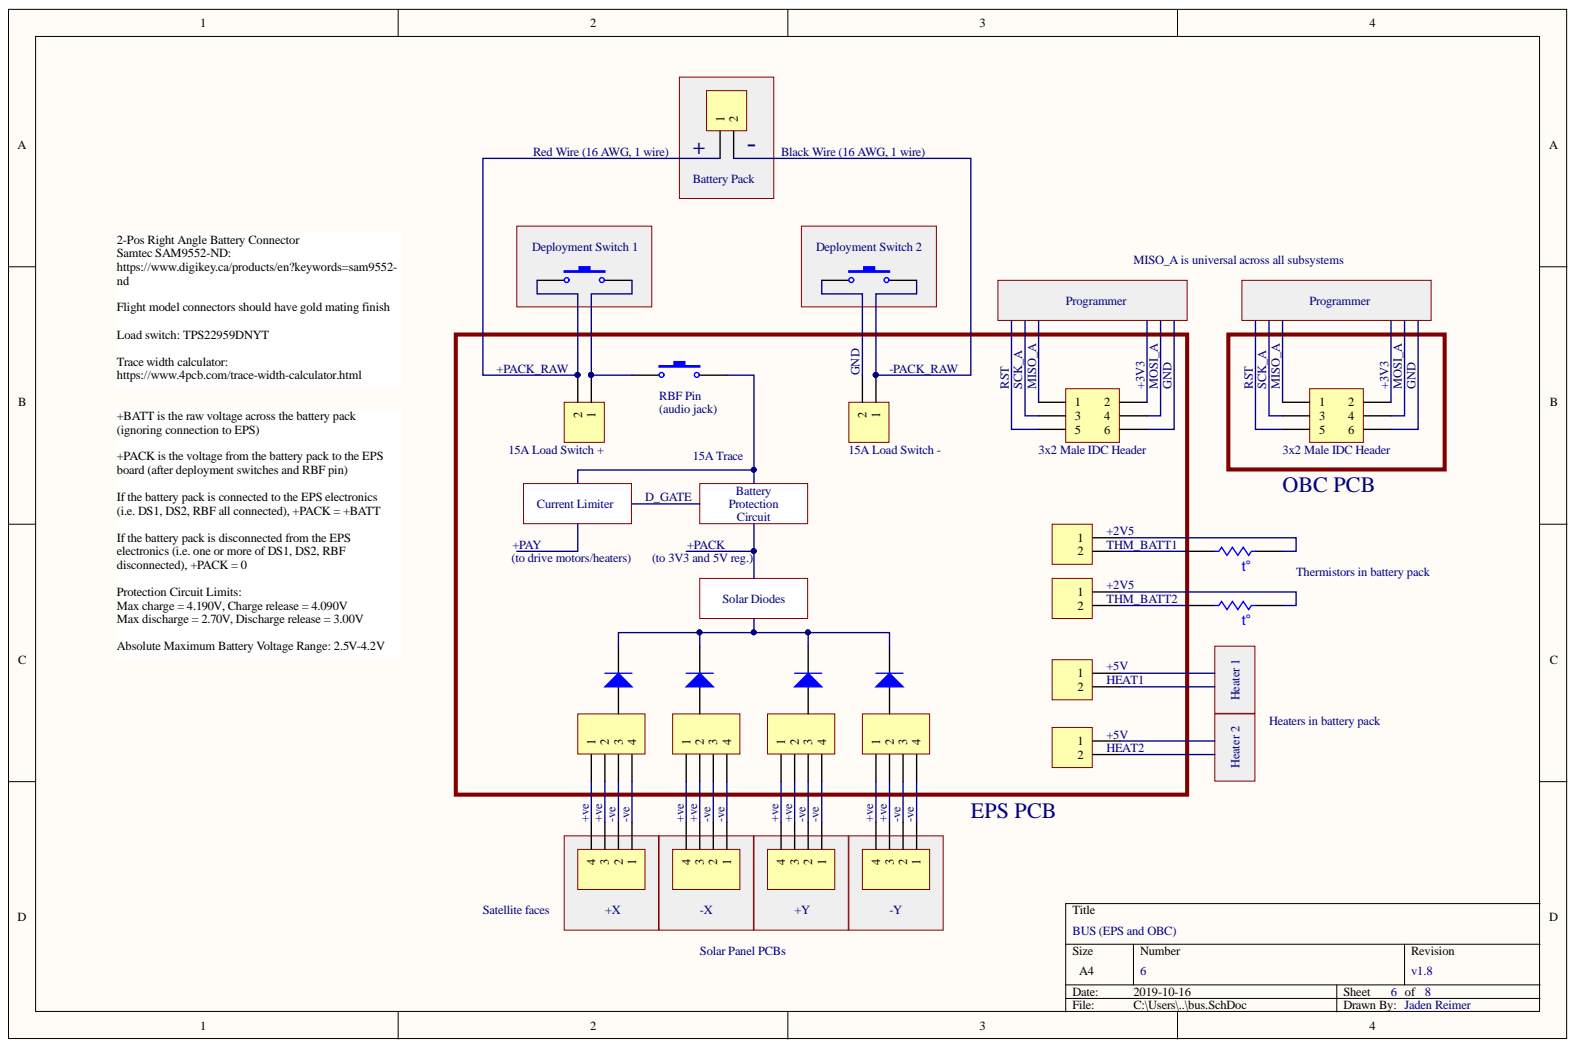
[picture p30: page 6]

2-Pos Right Angle Battery Connector
Samtec SAM9552-ND:
https://www.digikey.ca/products/en?keywords=sam9552-

MISO_A is universal across all subsystems

Flight model connectors should have gold mating finish

Trace width calculator:
https://www.4pcb.com/trace-width-calculator.html

+BATT is the raw voltage across the battery pack
(ignoring connection to EPS)

+PACK is the voltage from the battery pack to the EPS
board (after deployment switches and RBF pin)

If the battery pack is connected to the EPS electronics
(i.e. DS1, DS2, RBF all connected), +PACK = +BATT

If the battery pack is disconnected from the EPS
electronics (i.e. one or more of DS1, DS2, RBF
disconnected), +PACK = 0

Thermistors in battery pack

Protection Circuit Limits:
Max charge = 4.190V, Charge release = 4.090V
Max discharge = 2.70V, Discharge release = 3.00V

Absolute Maximum Battery Voltage Range: 2.5V-4.2V

Heaters in battery pack

Title
BUS (EPS and OBC)

Size A4 | Number 6 | Revision v1.8

Date: 2019-10-16 | Sheet 6 of 8
File: C:\Users\..\bus.SchDoc | Drawn By: Jaden Reimer

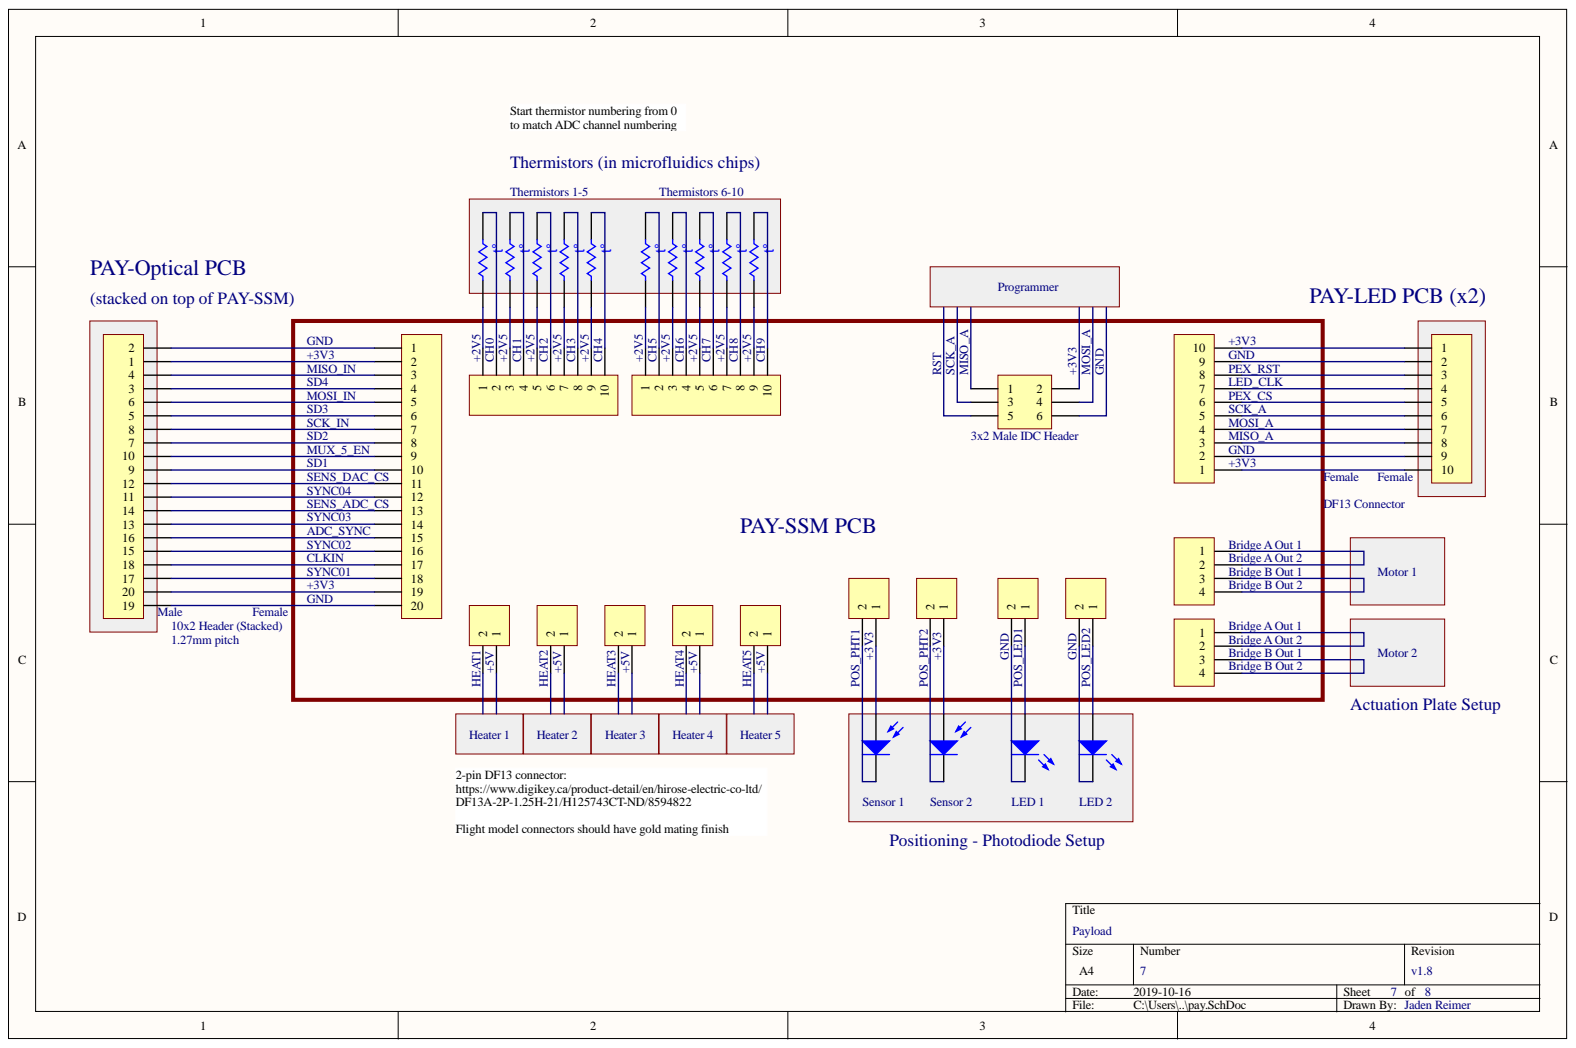
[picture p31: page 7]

Thermistors (in microfluidics chips)

(stacked on top of P

S Y N C04
SEN S_A D C_C S
S Y N C03
A D C_S Y N C

B ridge | A Out 2
B ridge B Out 1
B ridge | B Out 2

a/product-detail/en/hirose

ctors should have gold mating

Numbe r 7 | R evision v1. 8

: 2019-10-16 | She et 7 of 8
File : C:\Use rs\. .\pa y . S chDoc | D r a wn By: Jaden R eime r

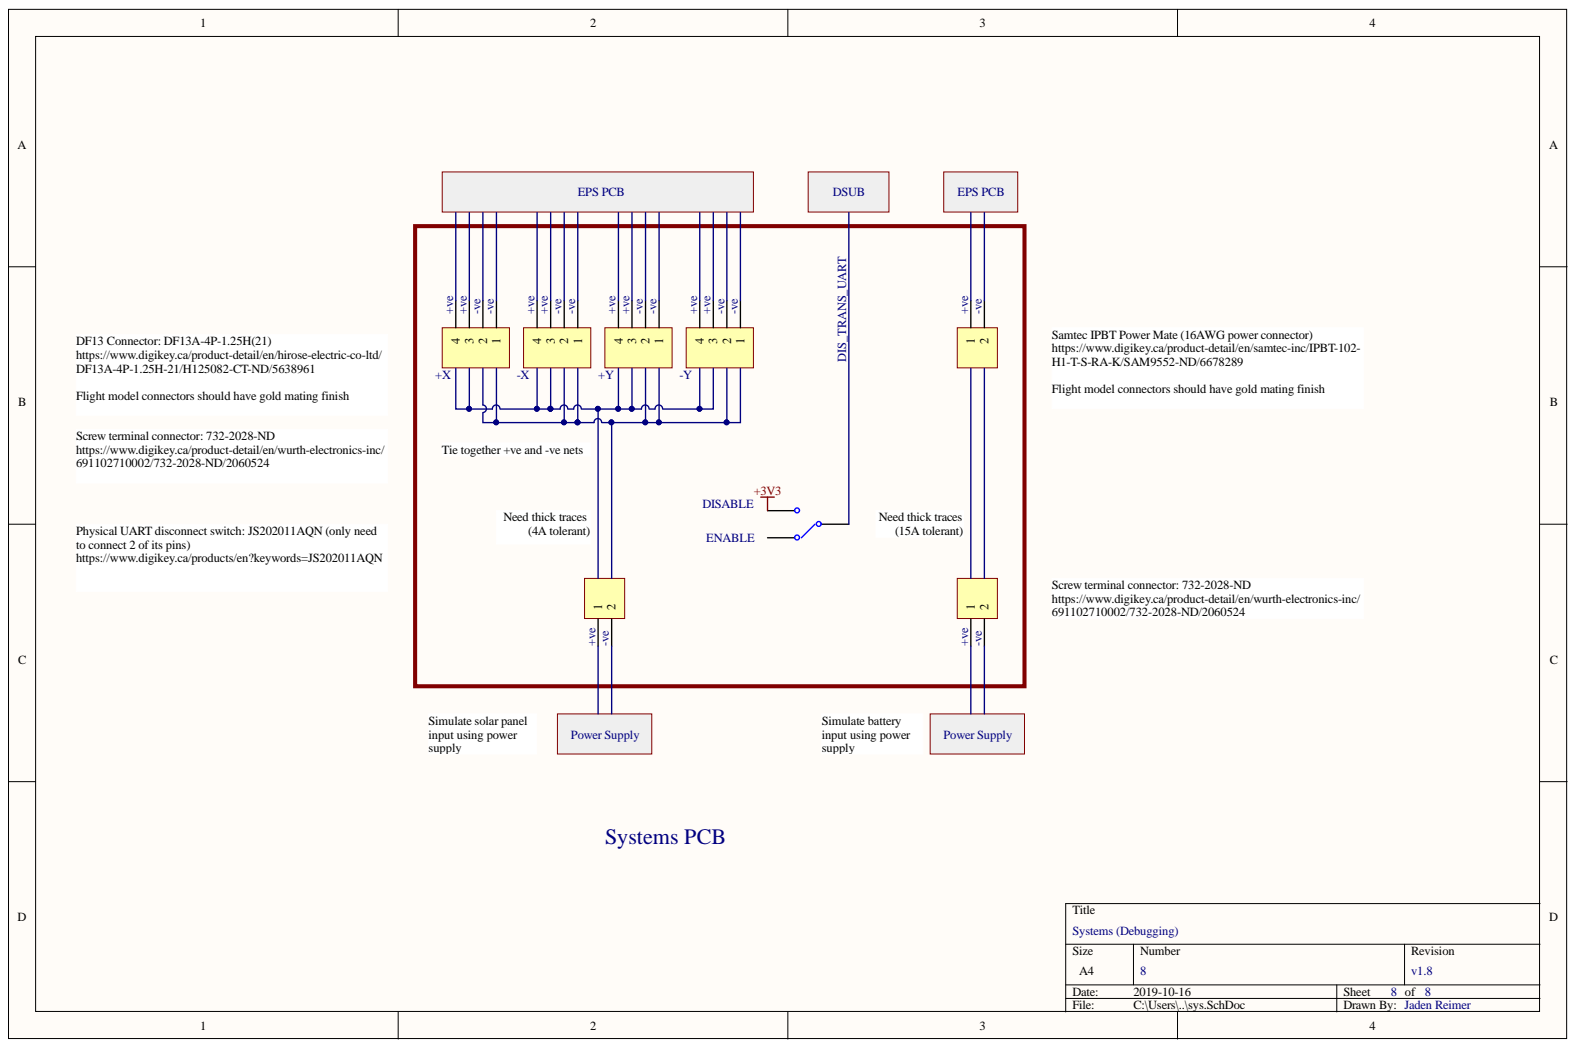
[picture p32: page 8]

DF13 Connector: DF13A-4P-1.25H(21)
https://www.digikey.ca/product-detail/en/hirose-electric-co-ltd/

Samtec IPBT Power Mate (16AWG power connector)
https://www.digikey.ca/product-detail/en/samtec-inc/IPBT-102-
H1-T-S-RA-K/SAM9552-ND/6678289

Flight model connectors should have gold mating finish

Screw terminal connector: 732-2028-ND
https://www.digikey.ca/product-detail/en/wurth-electronics-inc/

Tie together +ve and -ve nets

Physical UART disconnect switch: JS202011AQN (only need
to connect 2 of its pins)
https://www.digikey.ca/products/en?keywords=JS202011AQN

Size A4 | Number 8 | Revision v1.8

Date: 2019-10-16 | Sheet 8 of 8
File: C:\Users\..\sys.SchDoc | Drawn By: Jaden Reimer

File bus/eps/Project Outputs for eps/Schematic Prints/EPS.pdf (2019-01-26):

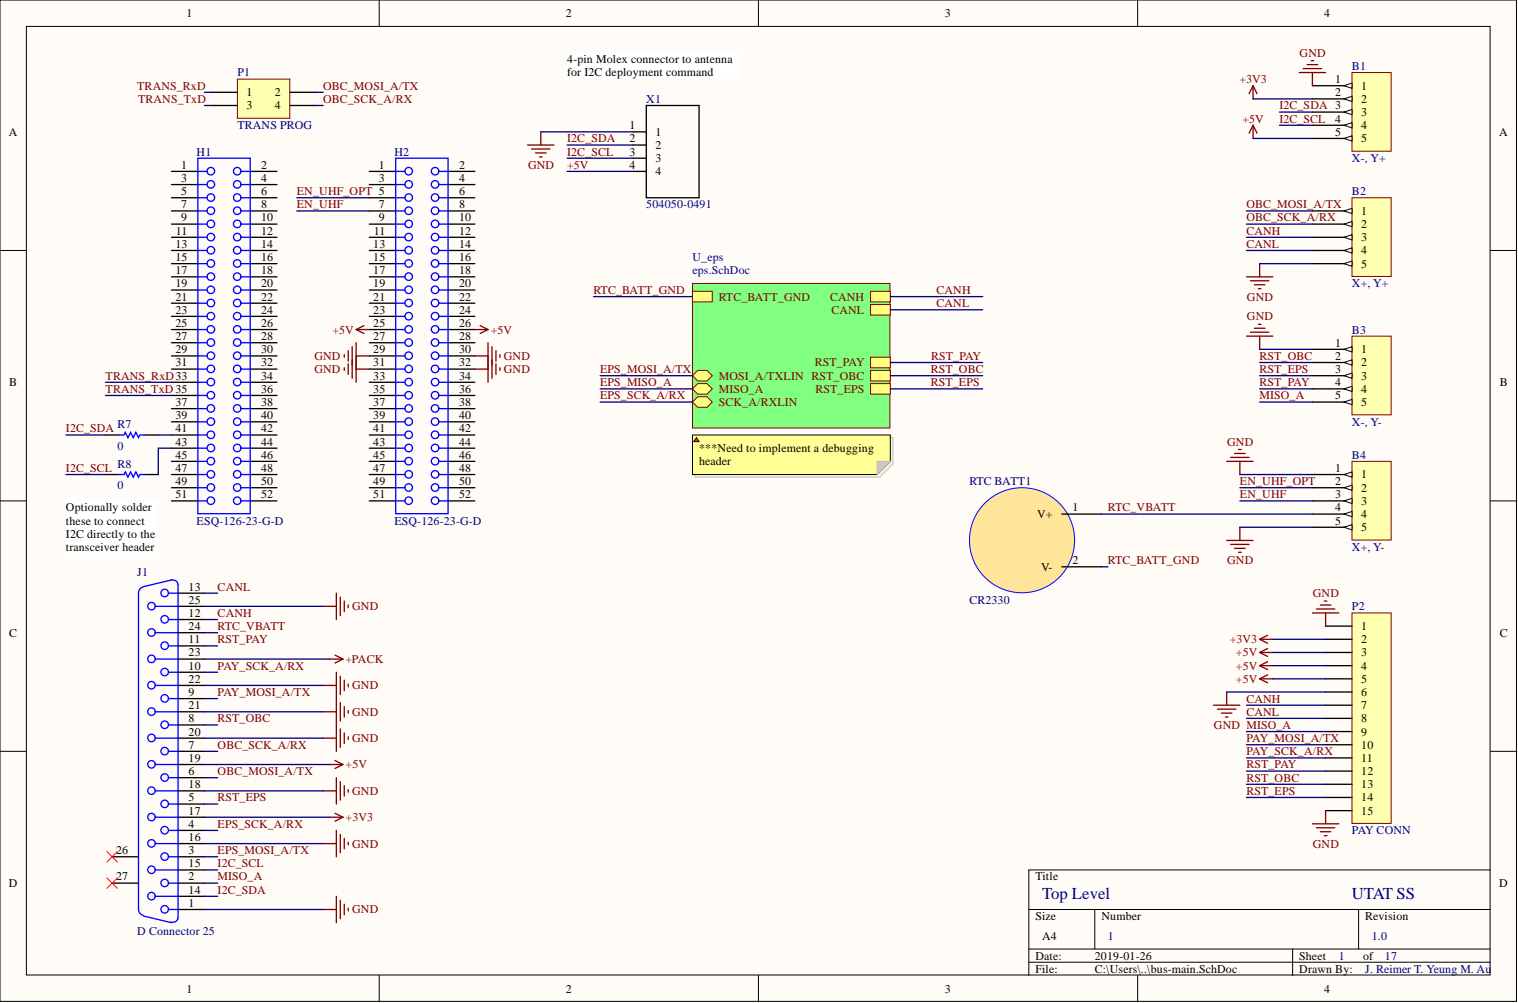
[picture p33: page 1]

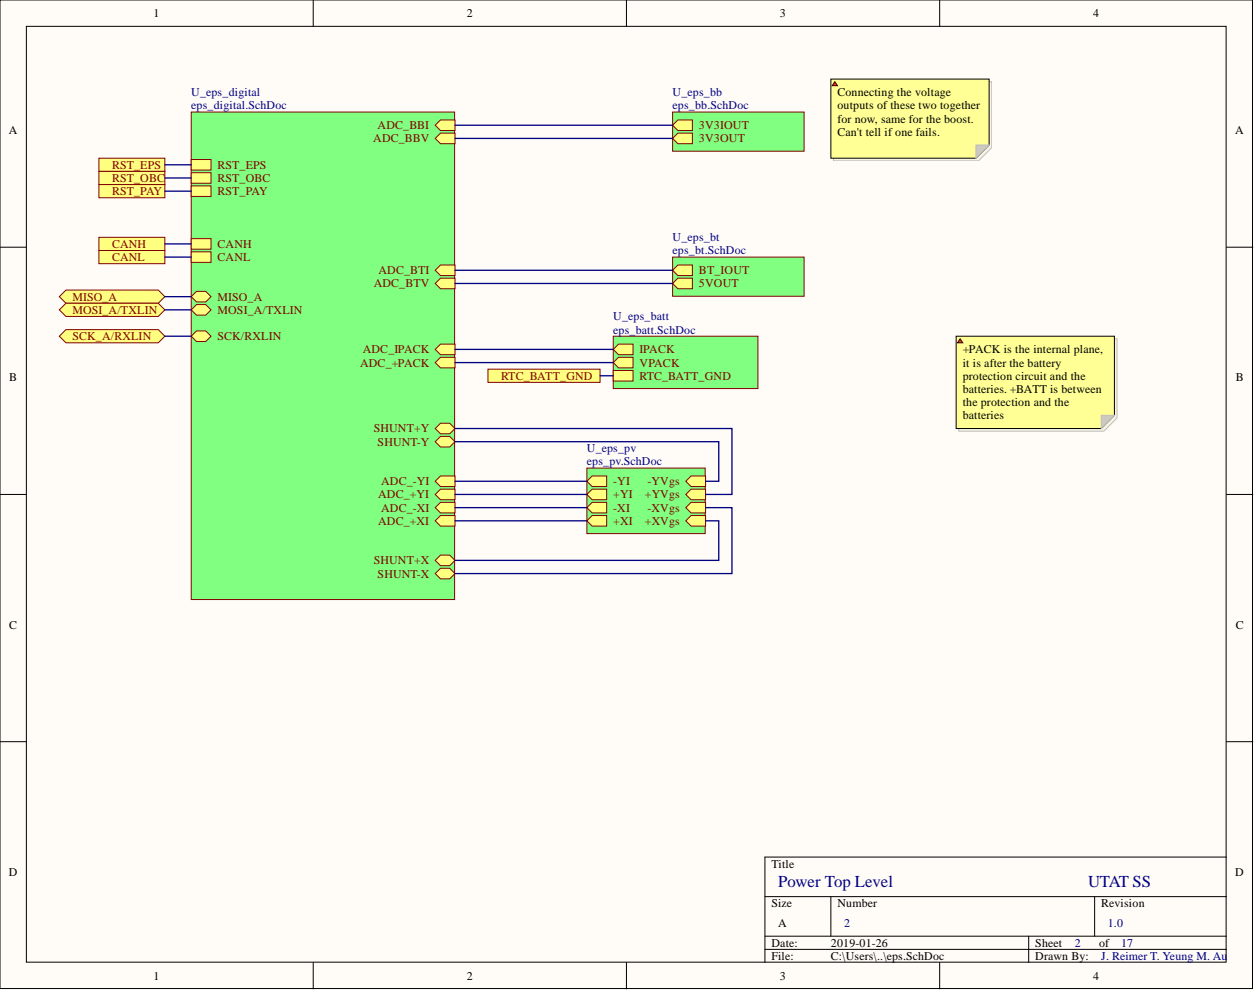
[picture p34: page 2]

Connecting the voltage
outputs of these two together
for now, same for the boost.
Can't tell if one fails.

+PACK is the internal plane,
it is after the battery
protection circuit and the
batteries. +BATT is between
the protection and the
batteries

+YI +YVgs

+XI +XVgs

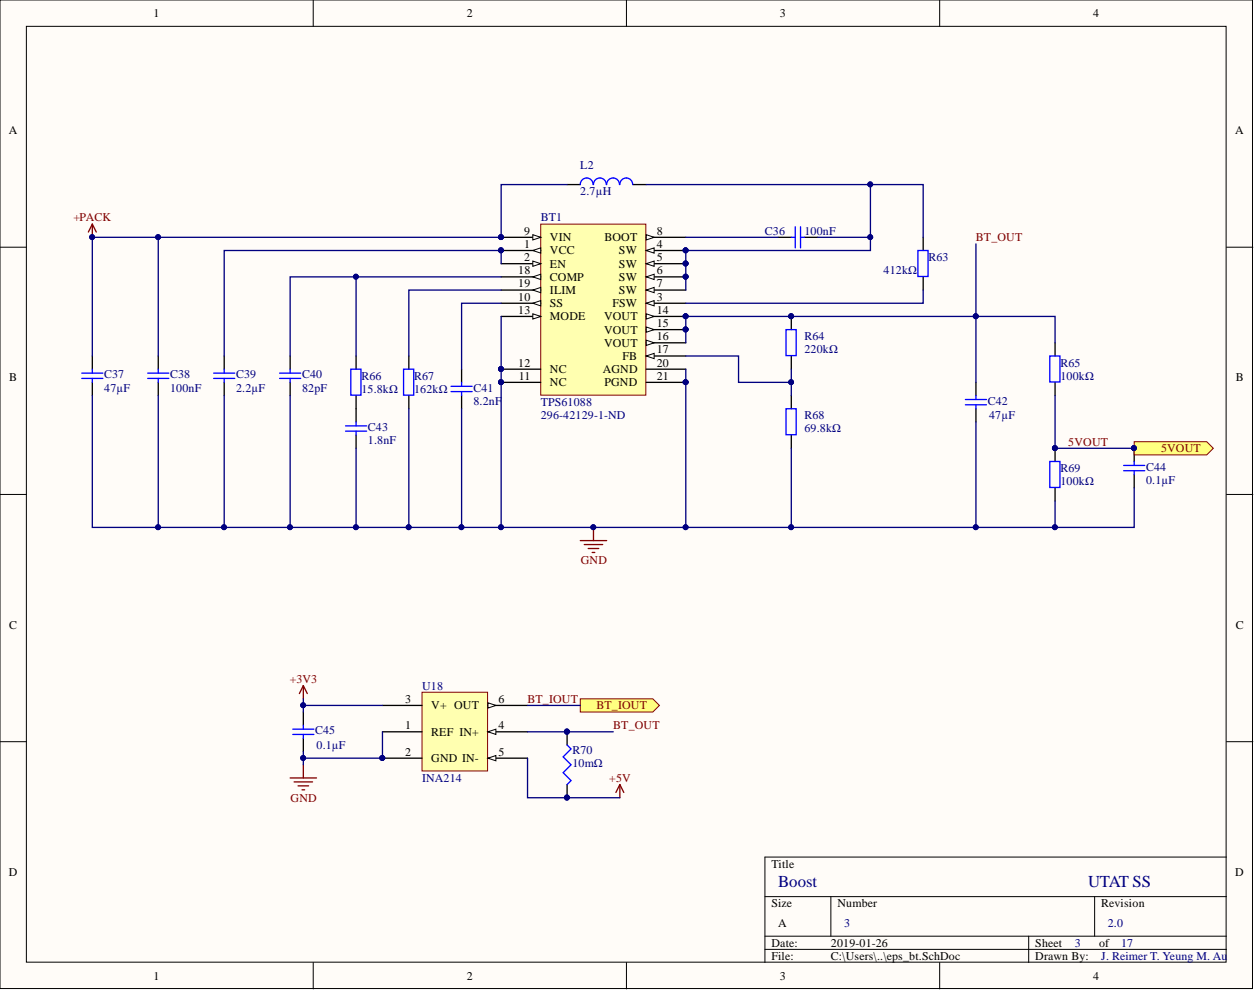
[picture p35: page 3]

ILIM 19

REF 1

0.1µF | GND 2

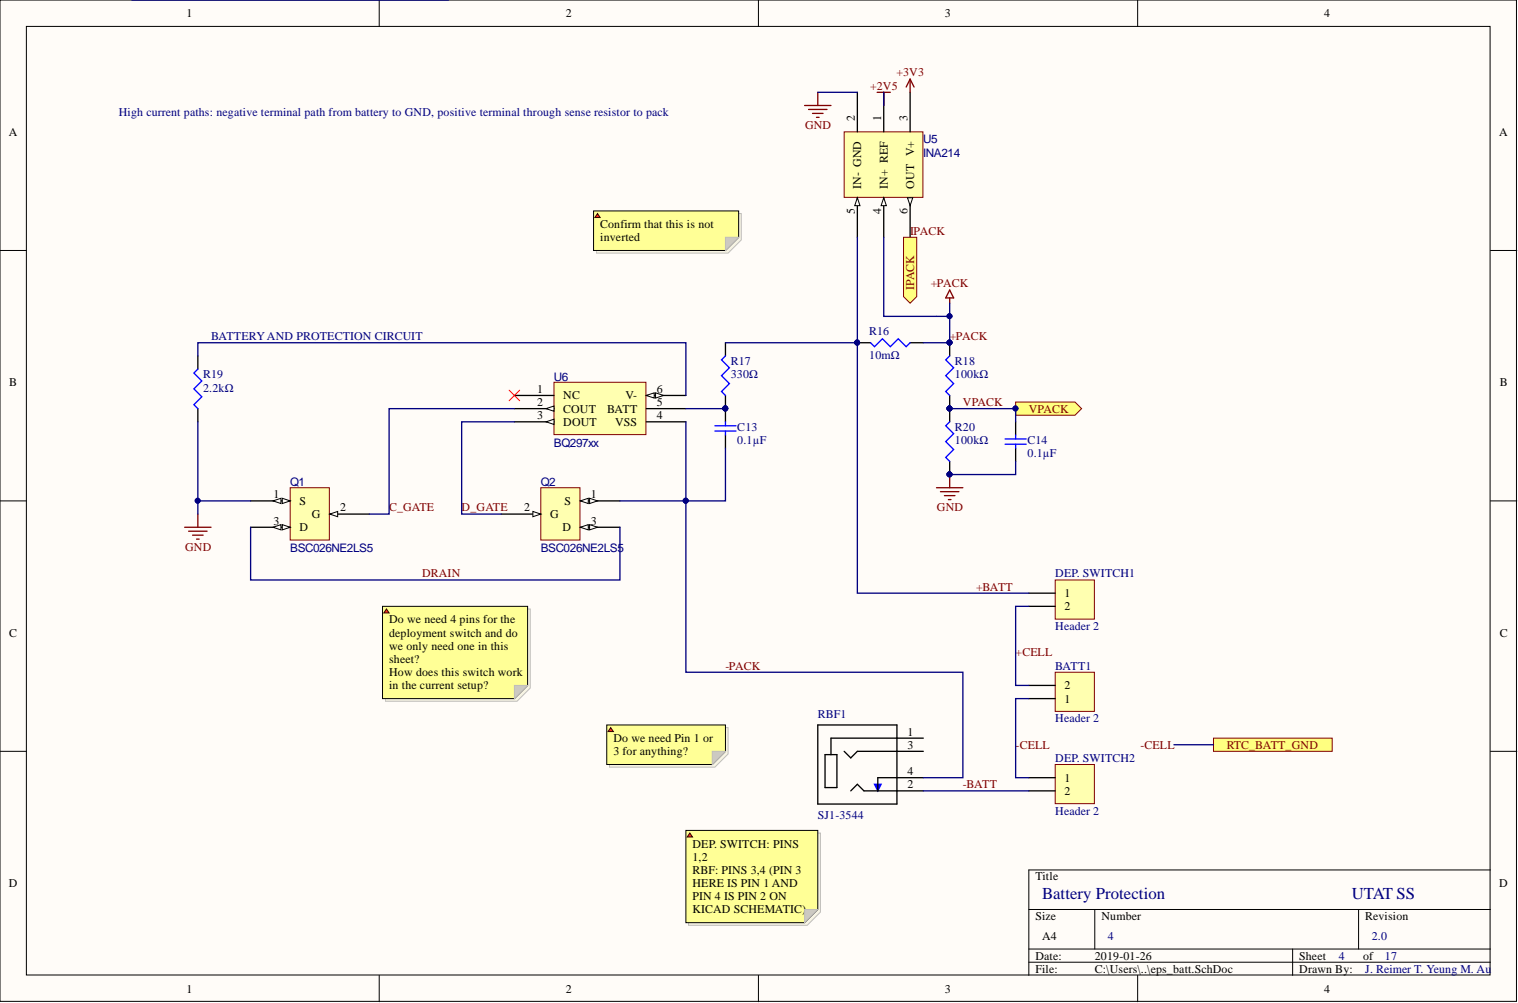
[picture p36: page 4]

High current paths: negative terminal path from battery to GND, positive terminal through sense resistor to pack

Confirm that this is not
inverted

BATTERY AND PROTECTION CIRCUIT

Do we need 4 pins for the
deployment switch and do
we only need one in this
sheet?
How does this switch work
in the current setup?

Do we need Pin 1 or
3 for anything?

DEP. SWITCH: PINS
RBF: PINS 3,4 (PIN 3
HERE IS PIN 1 AND
PIN 4 IS PIN 2 ON
KICAD SCHEMATIC)

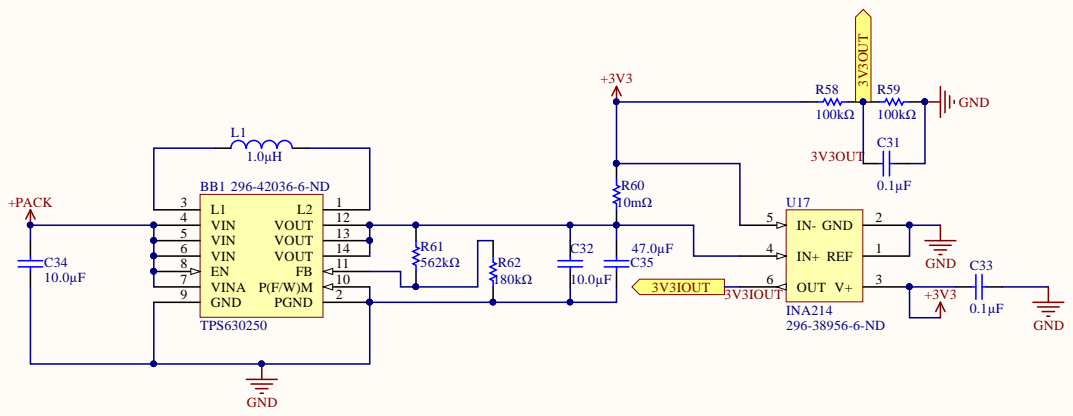
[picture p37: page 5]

5 | 1 3 | 4 7.0 µ F | 4 | 1
6 | 1 4

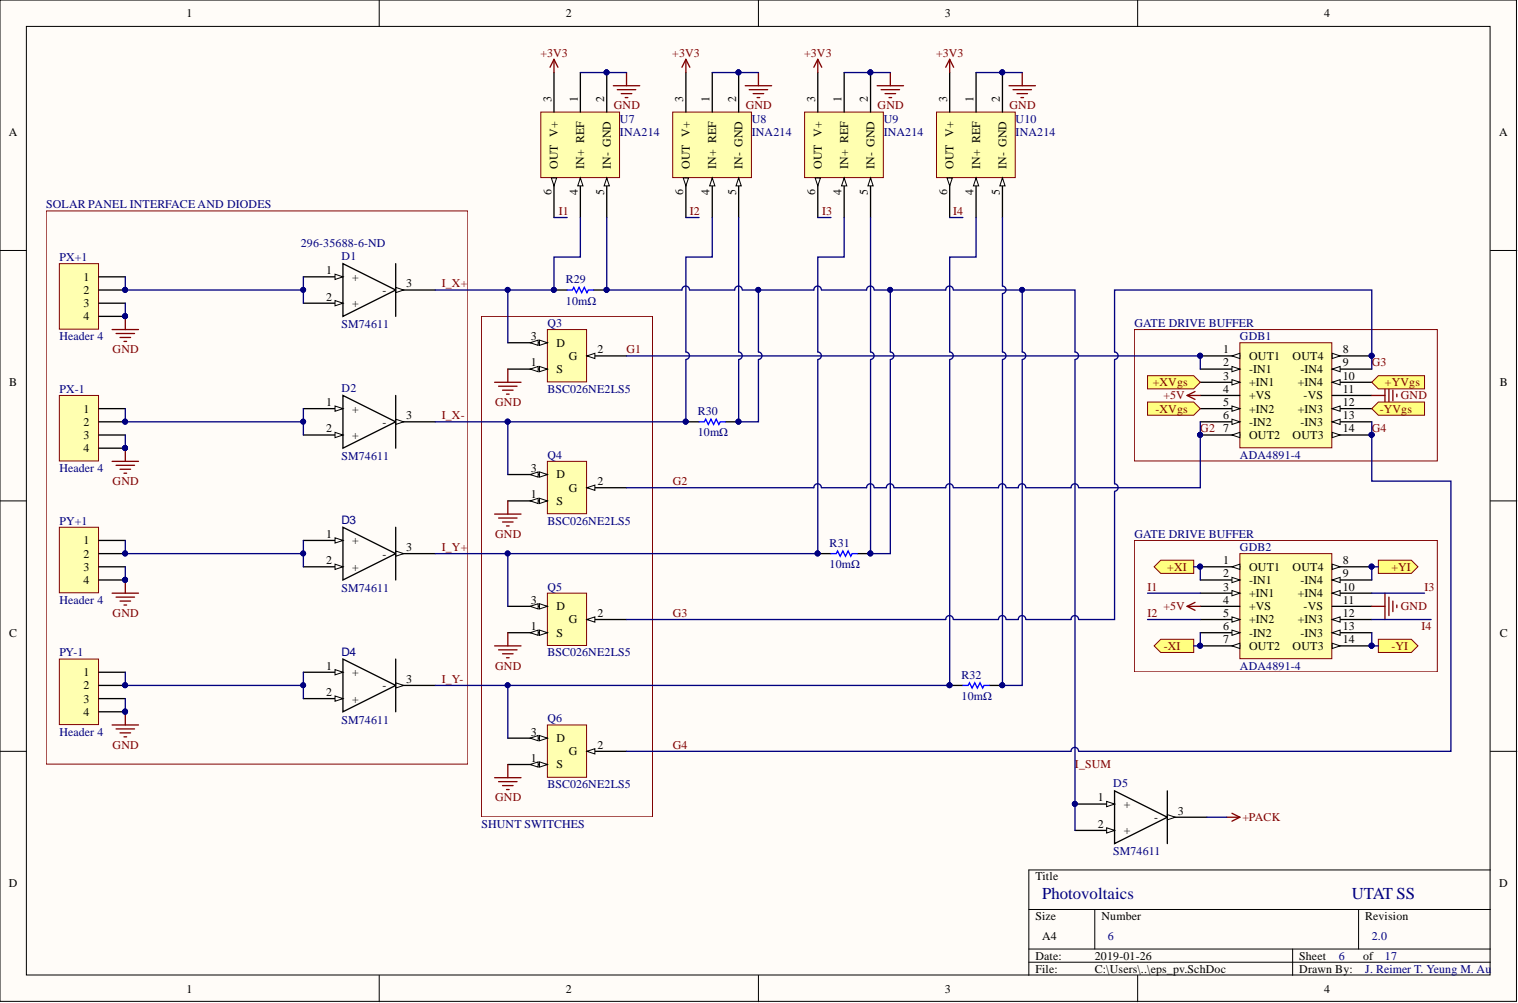
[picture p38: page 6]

SOLAR PANEL INTERFACE AND DIODES

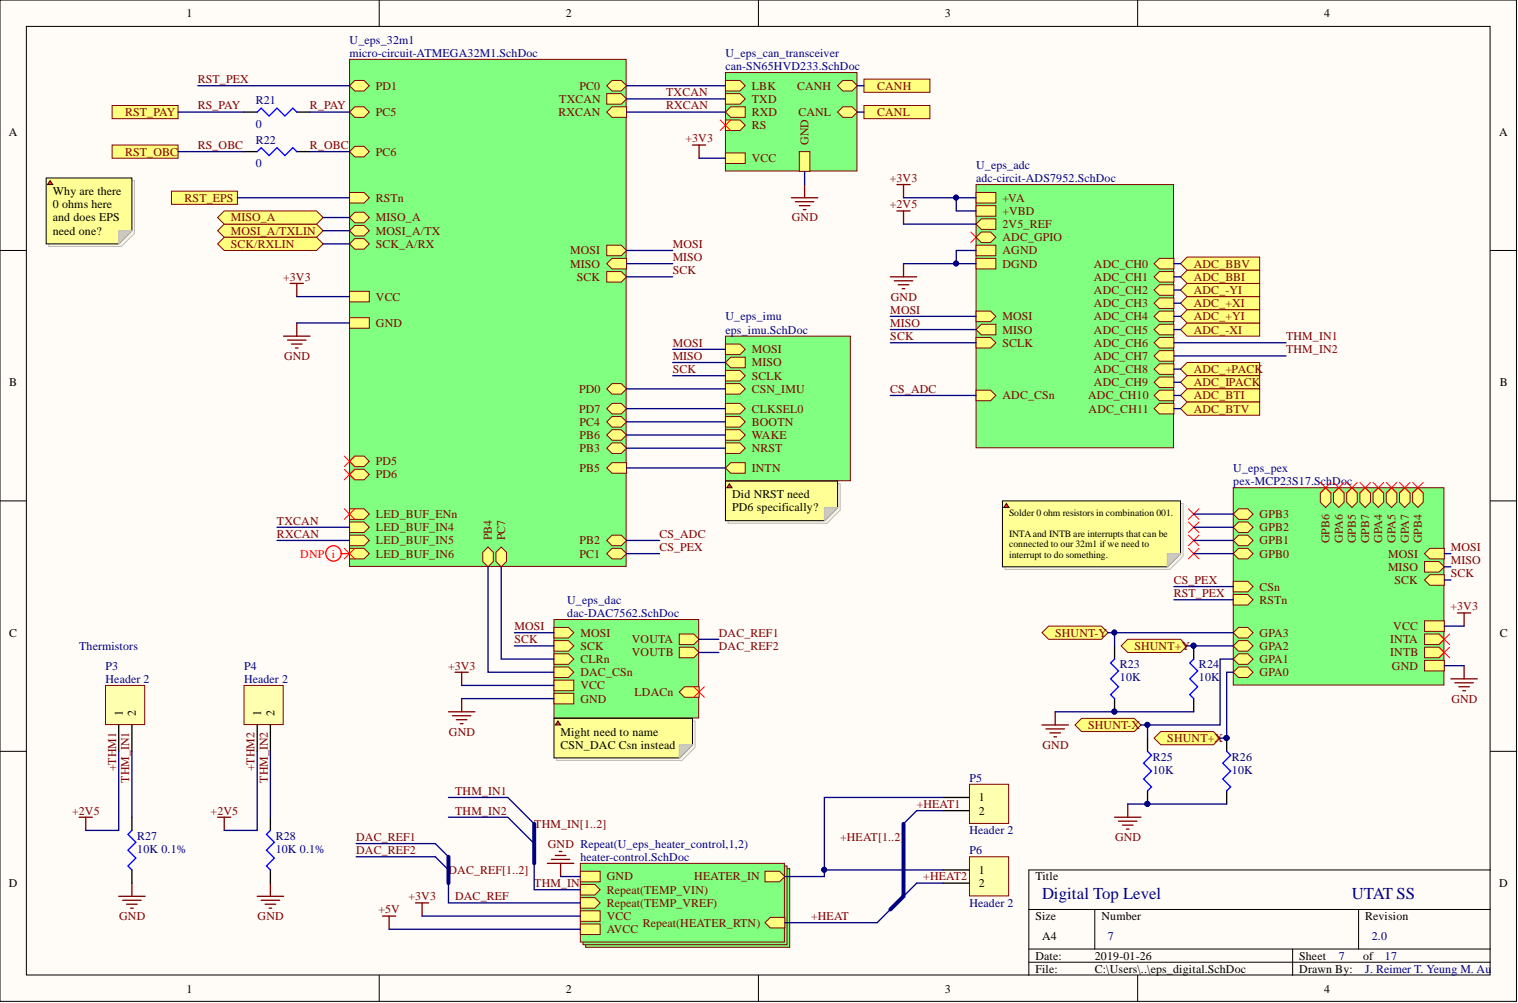
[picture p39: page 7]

Solder 0 ohm resistors in combination 001.

INTAand INTB are interrupts that can be
connected to our 32m1 if we need to
interrupt to do something.

Might need to name
CSN_DAC Csn instead

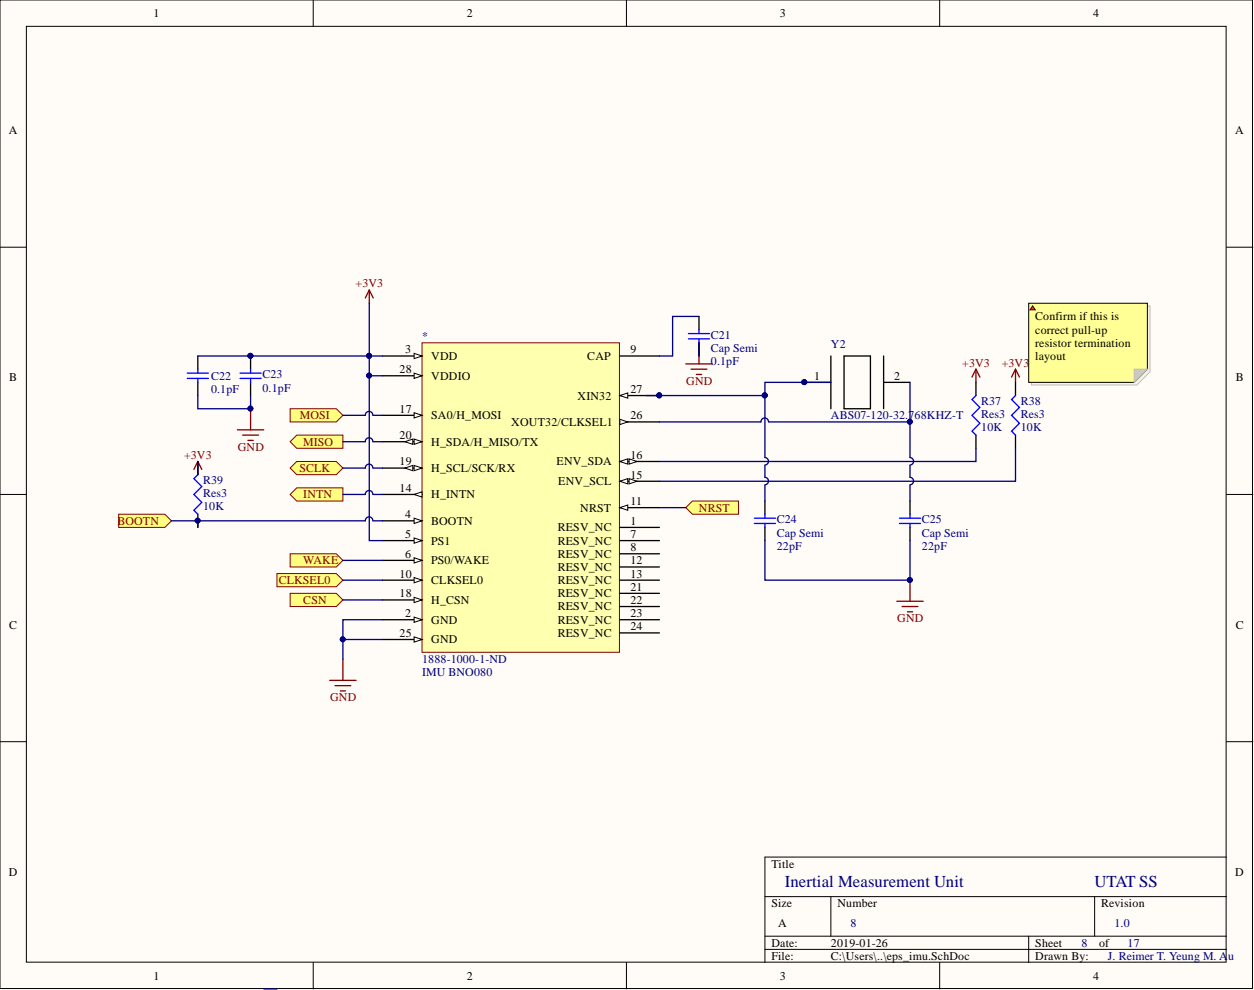
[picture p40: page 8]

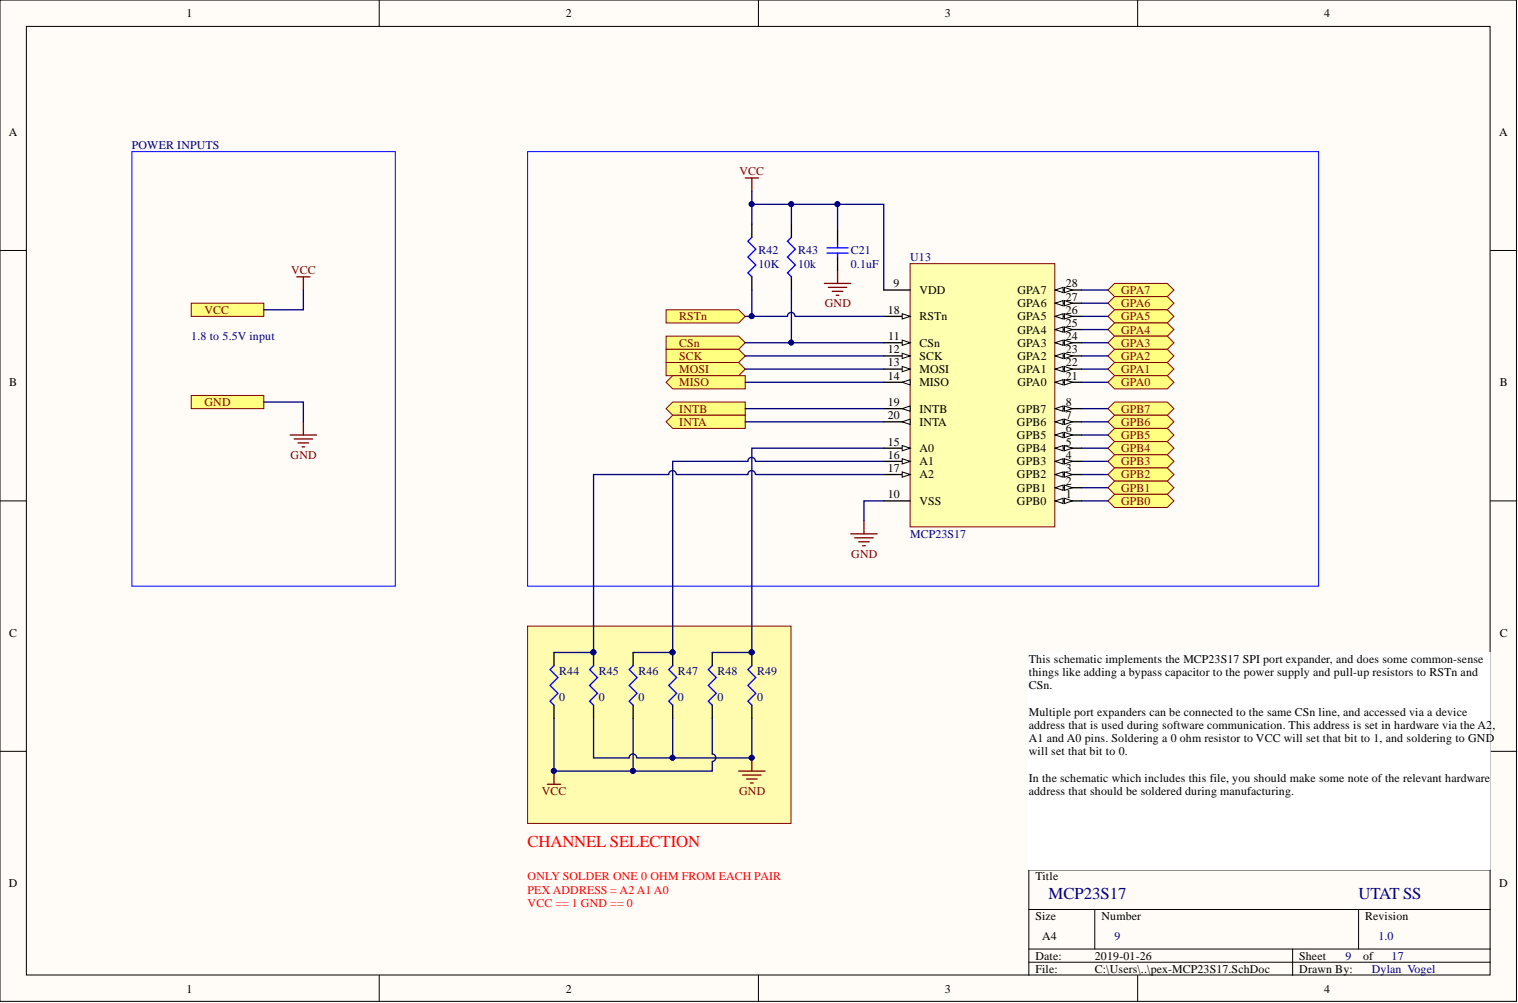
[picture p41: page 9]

This schematic implements the MCP23S17 SPI port expander, and does some common-sense
things like adding a bypass capacitor to the power supply and pull-up resistors to RSTn and
CSn.

Multiple port expanders can be connected to the same CSn line, and accessed via a device
address that is used during software communication. This address is set in hardware via the A2,
A1 and A0 pins. Soldering a 0 ohm resistor to VCC will set that bit to 1, and soldering to GND
will set that bit to 0.

In the schematic which includes this file, you should make some note of the relevant hardware
address that should be soldered during manufacturing.

ONLY SOLDER ONE 0 OHM FROM EACH PAIR
UTAT SS PEX ADDRESS = A2 A1 A0
VCC == 1 GND == 0

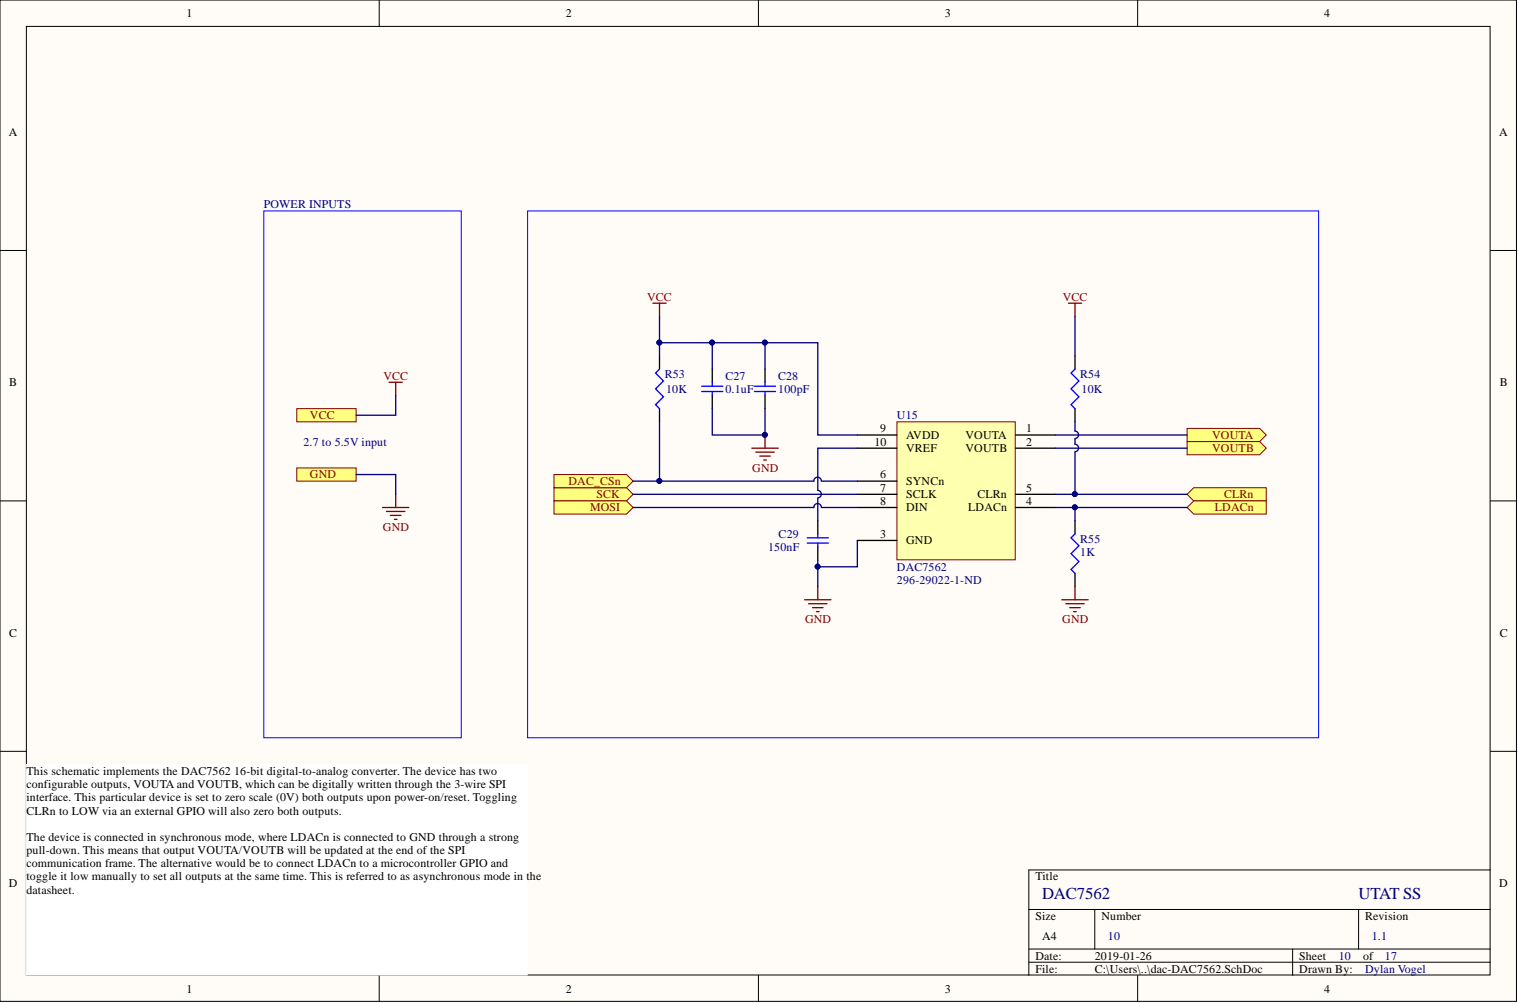
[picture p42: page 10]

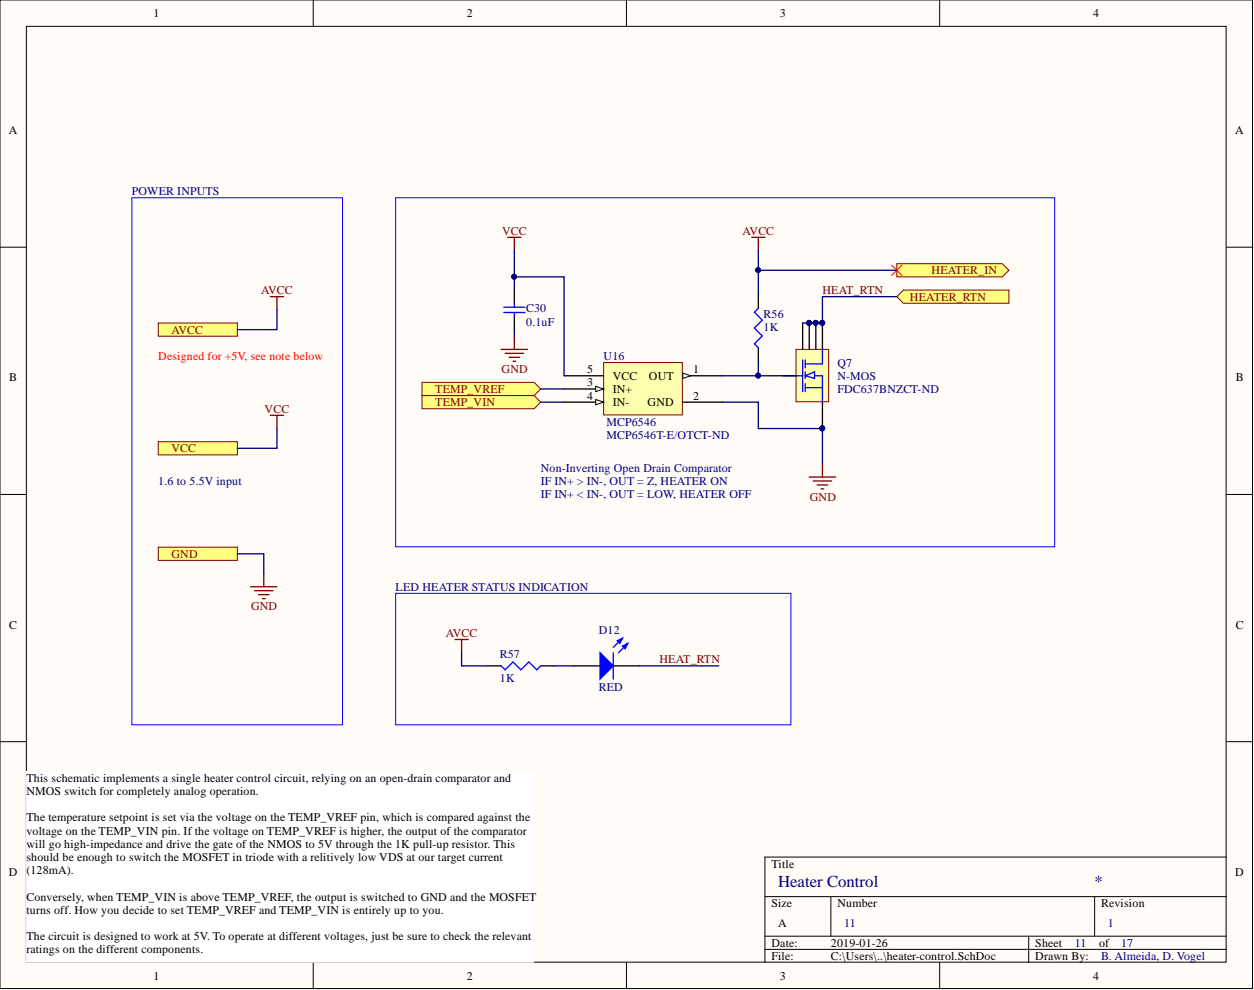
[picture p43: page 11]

Designed for +5V, see note below

Non-Inverting Open Drain Comparator
IF IN+ > IN-, OUT = Z, HEATER ON
IF IN+ < IN-, OUT = LOW, HEATER OFF

LED HEATER STATUS INDICATION

This schematic implements a single heater control circuit, relying on an open-drain comparator and
NMOS switch for completely analog operation.

The temperature setpoint is set via the voltage on the TEMP_VREF pin, which is compared against the
voltage on the TEMP_VIN pin. If the voltage on TEMP_VREF is higher, the output of the comparator
will go high-impedance and drive the gate of the NMOS to 5V through the 1K pull-up resistor. This
should be enough to switch the MOSFET in triode with a relitively low VDS at our target current

Conversely, when TEMP_VIN is above TEMP_VREF, the output is switched to GND and the MOSFET
turns off. How you decide to set TEMP_VREF and TEMP_VIN is entirely up to you.

The circuit is designed to work at 5V. To operate at different voltages, just be sure to check the relevant
ratings on the different components.

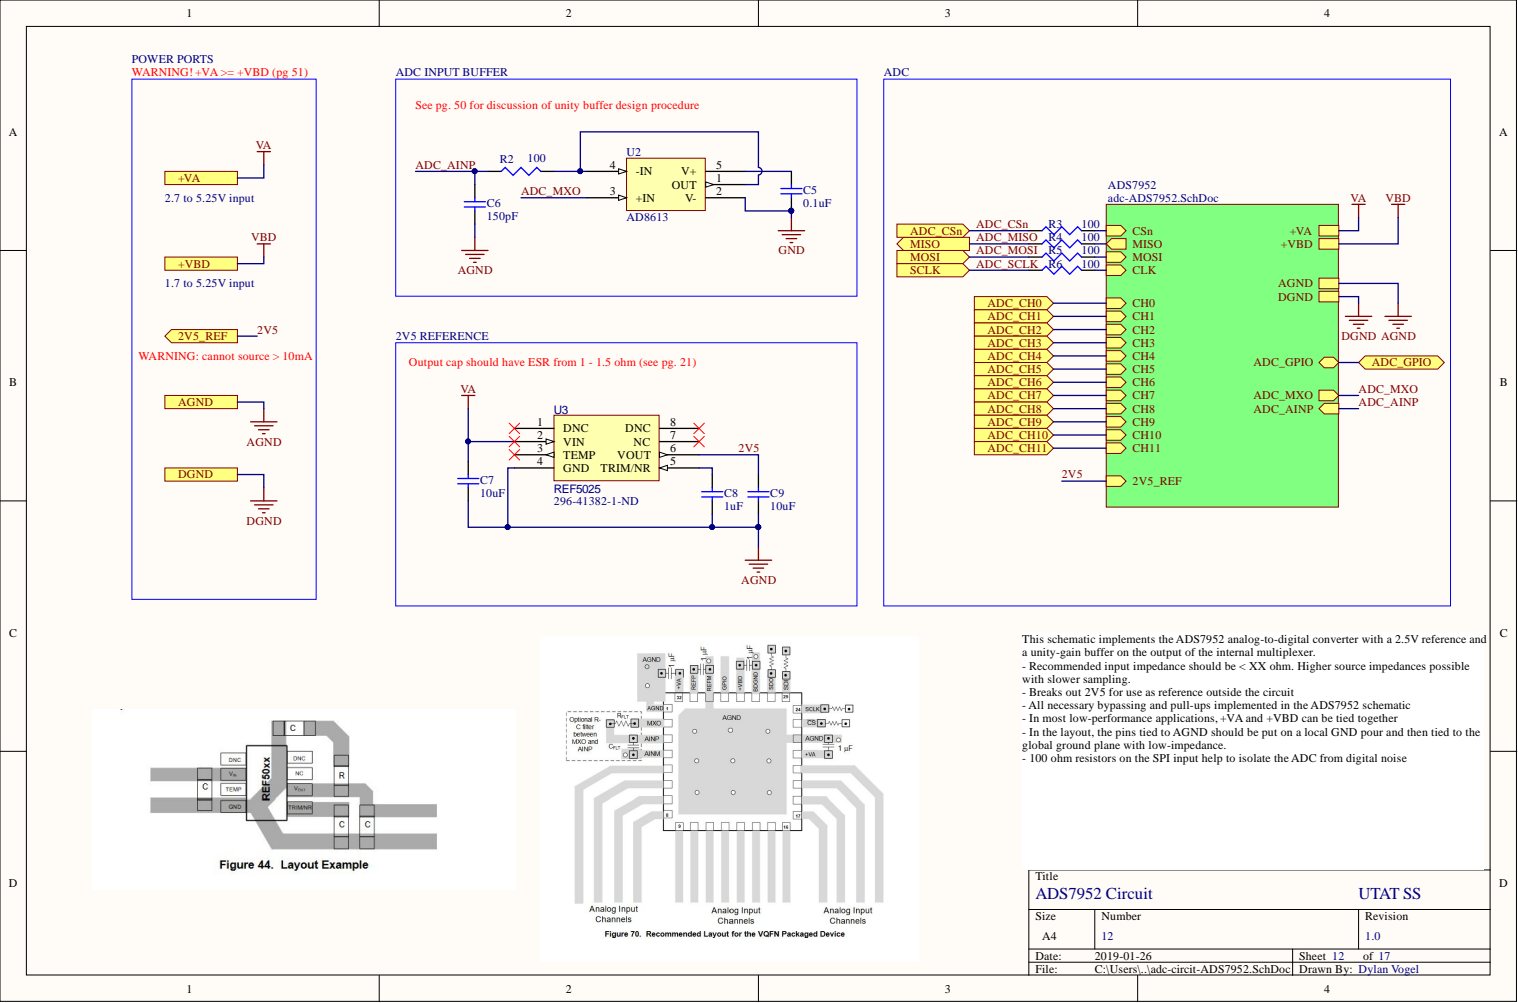
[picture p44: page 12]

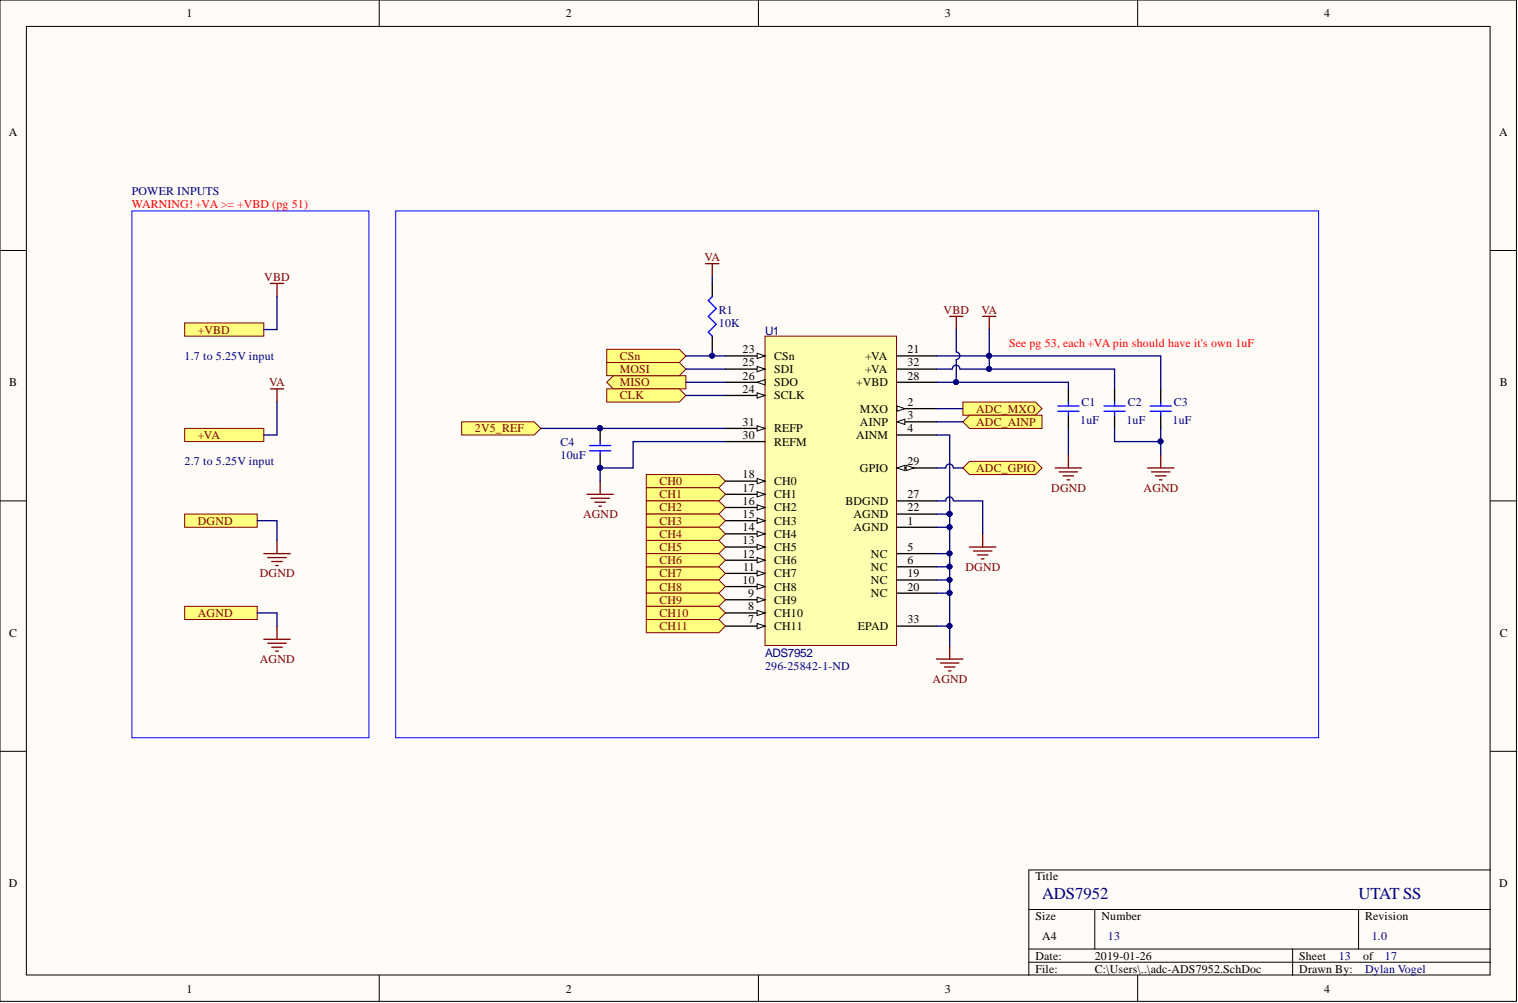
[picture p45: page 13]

3 2
2 8

2 7
2 2

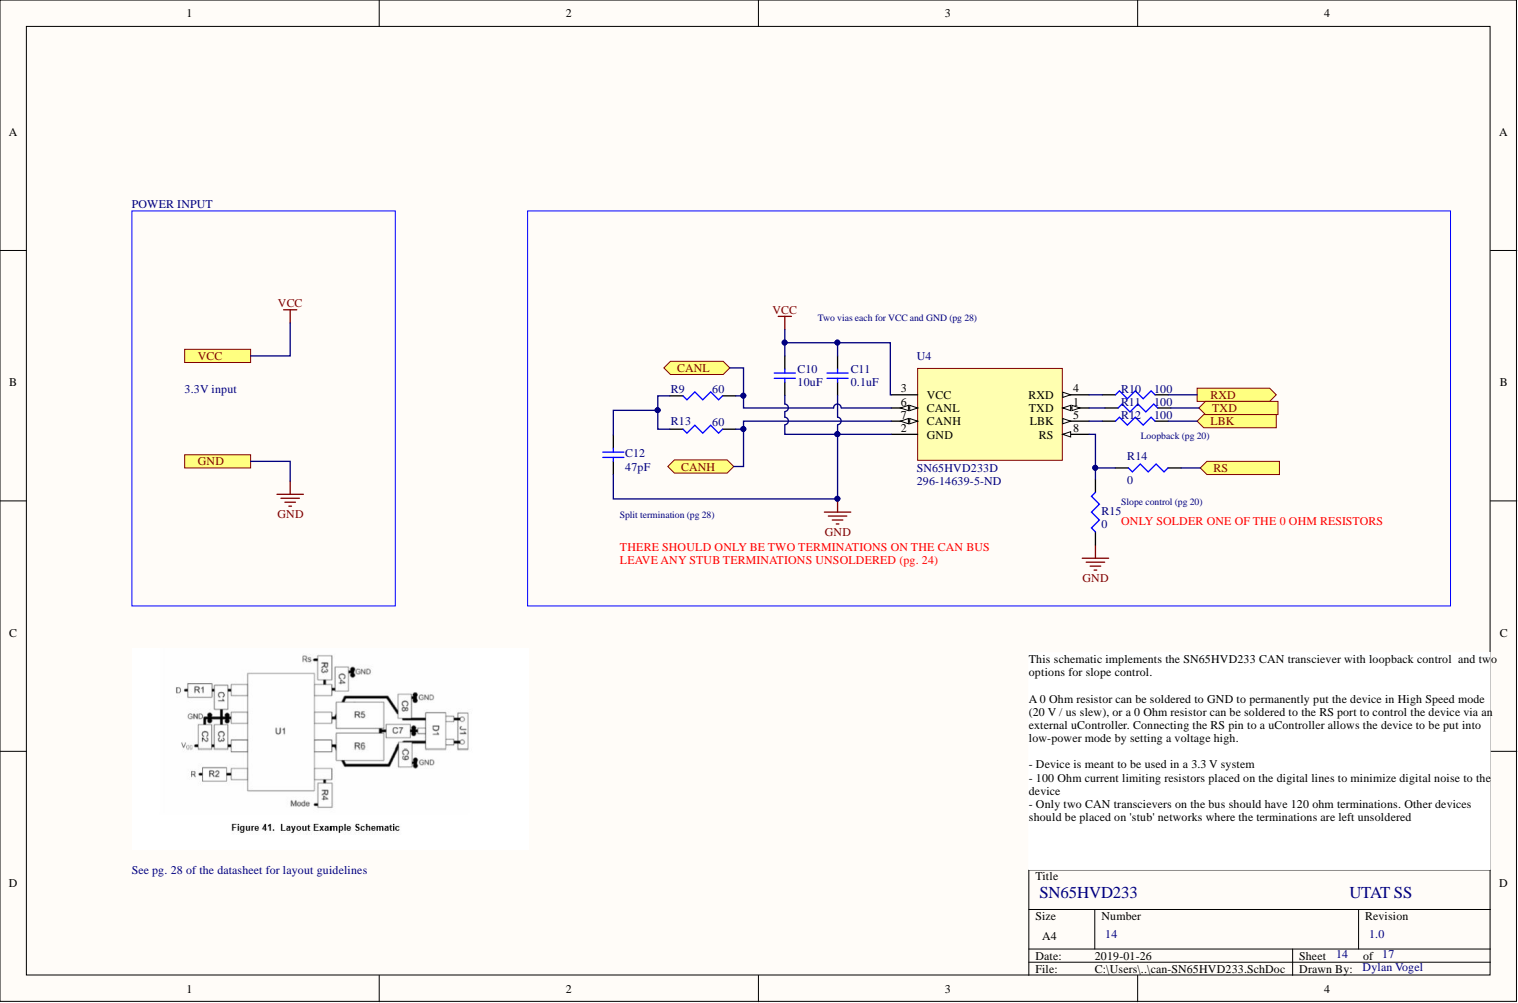
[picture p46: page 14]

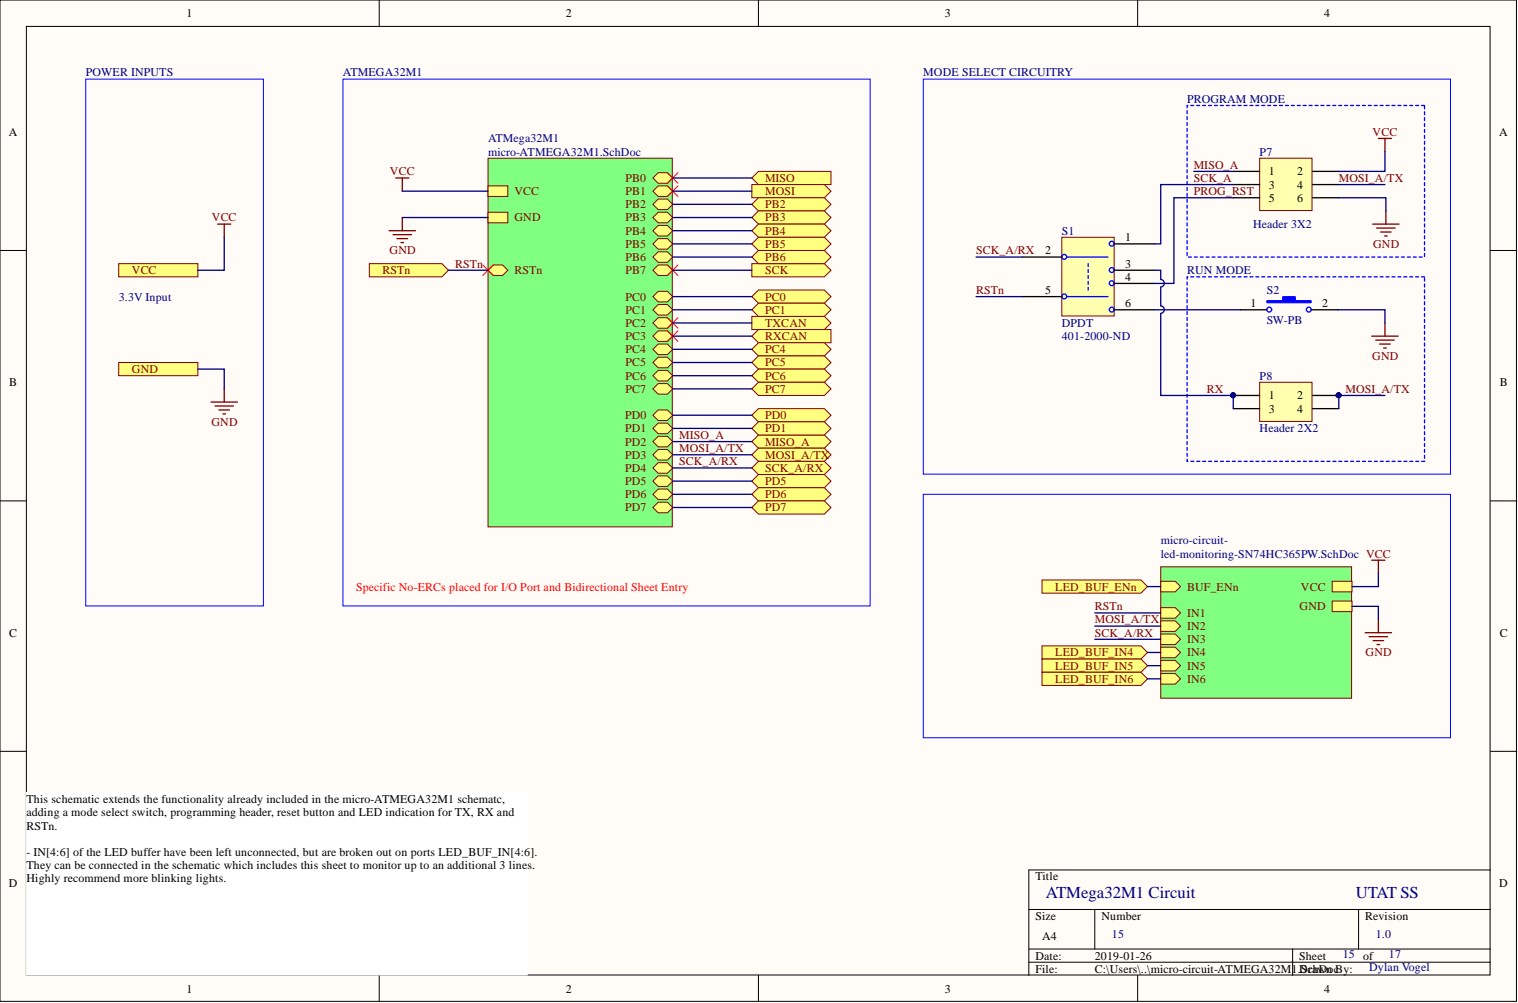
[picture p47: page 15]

hey can be co

uffer have been left u
he schemat

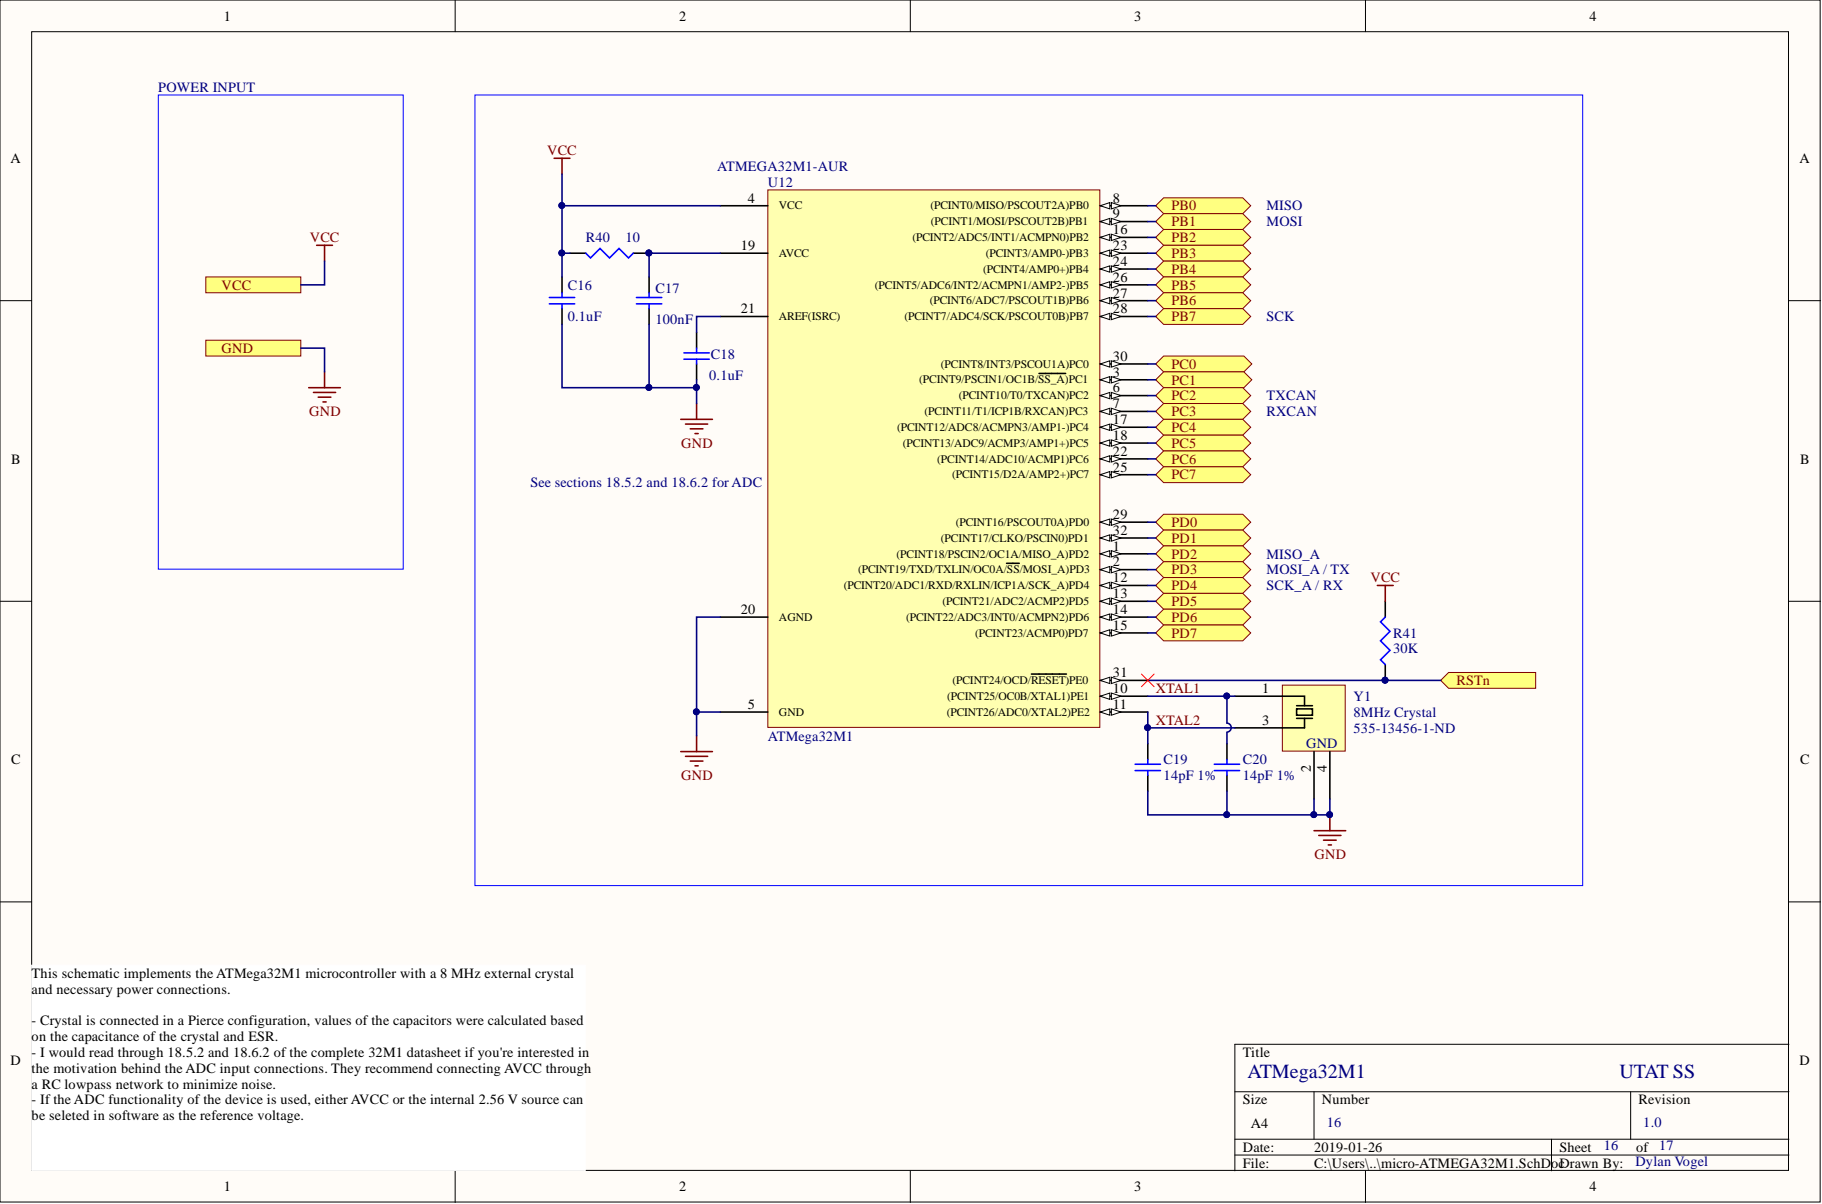
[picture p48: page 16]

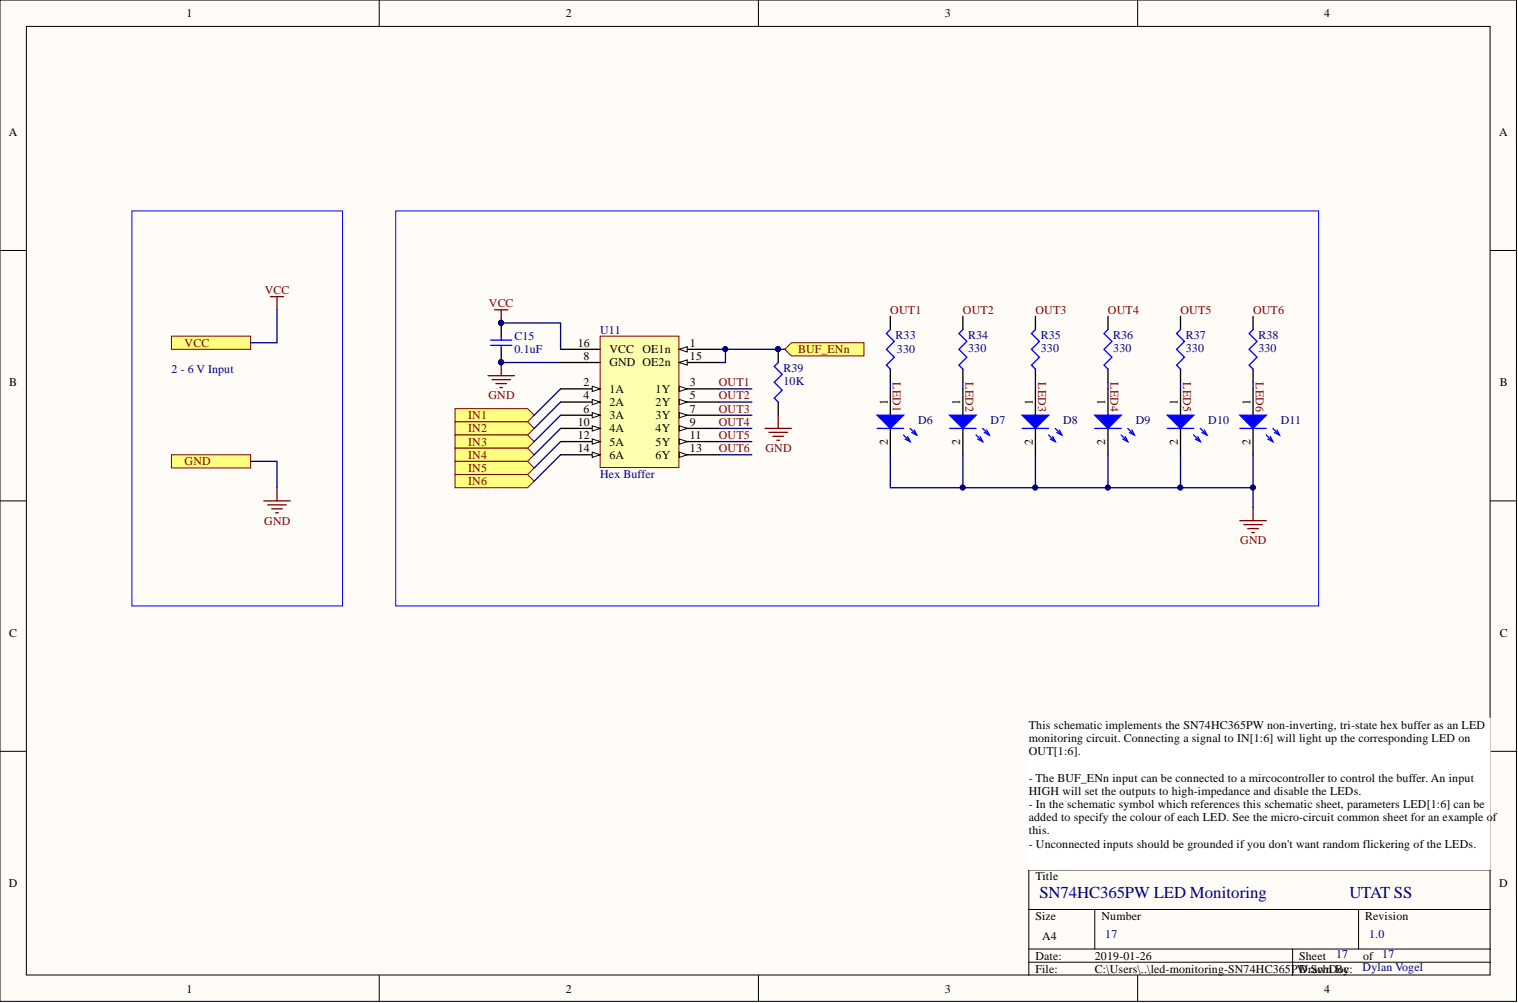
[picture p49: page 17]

heet for an examp

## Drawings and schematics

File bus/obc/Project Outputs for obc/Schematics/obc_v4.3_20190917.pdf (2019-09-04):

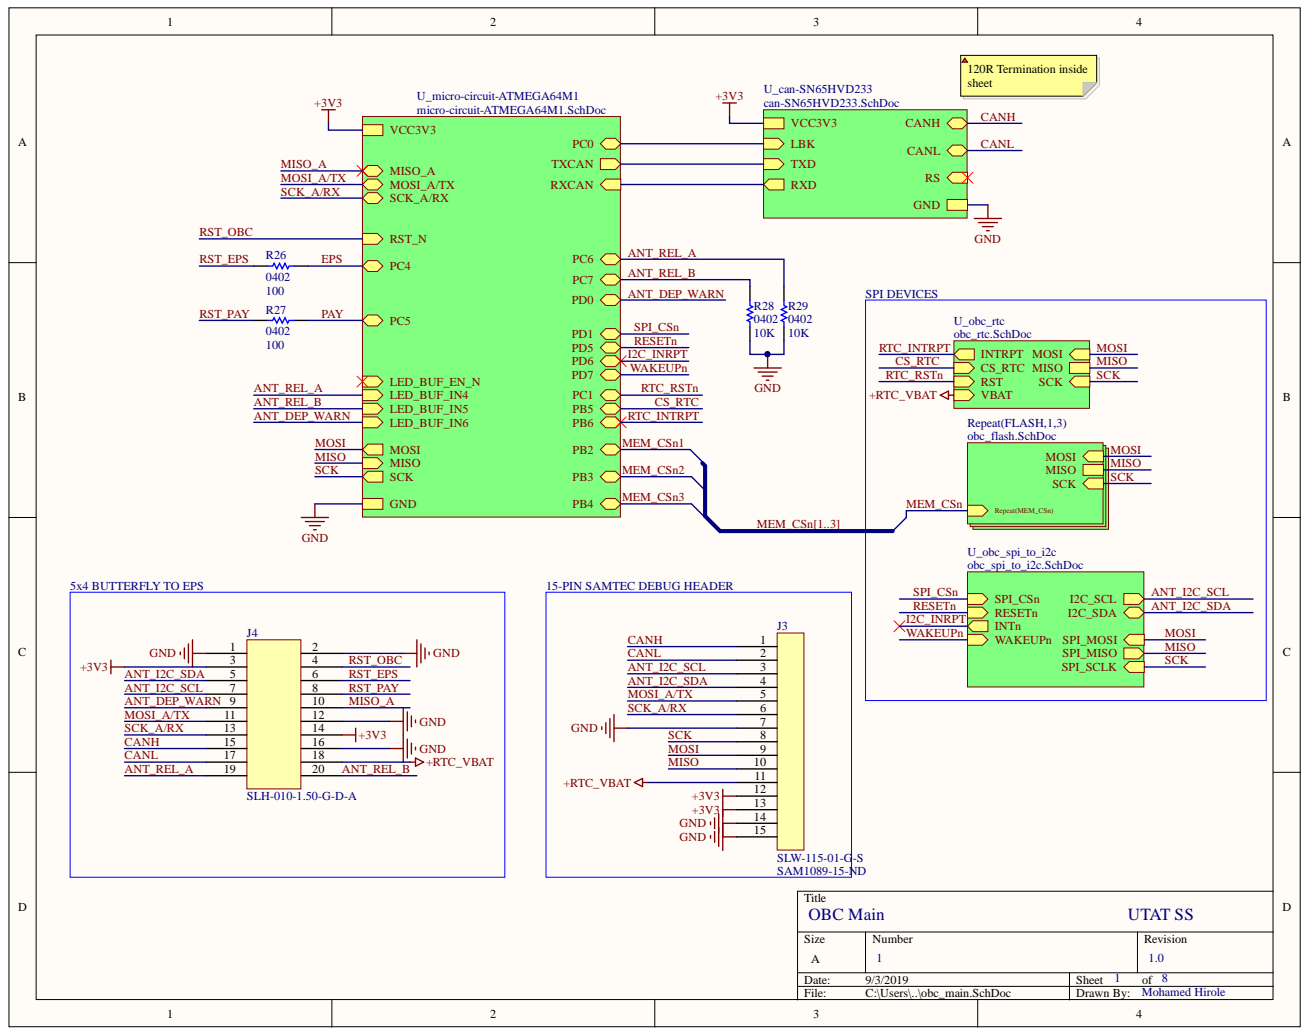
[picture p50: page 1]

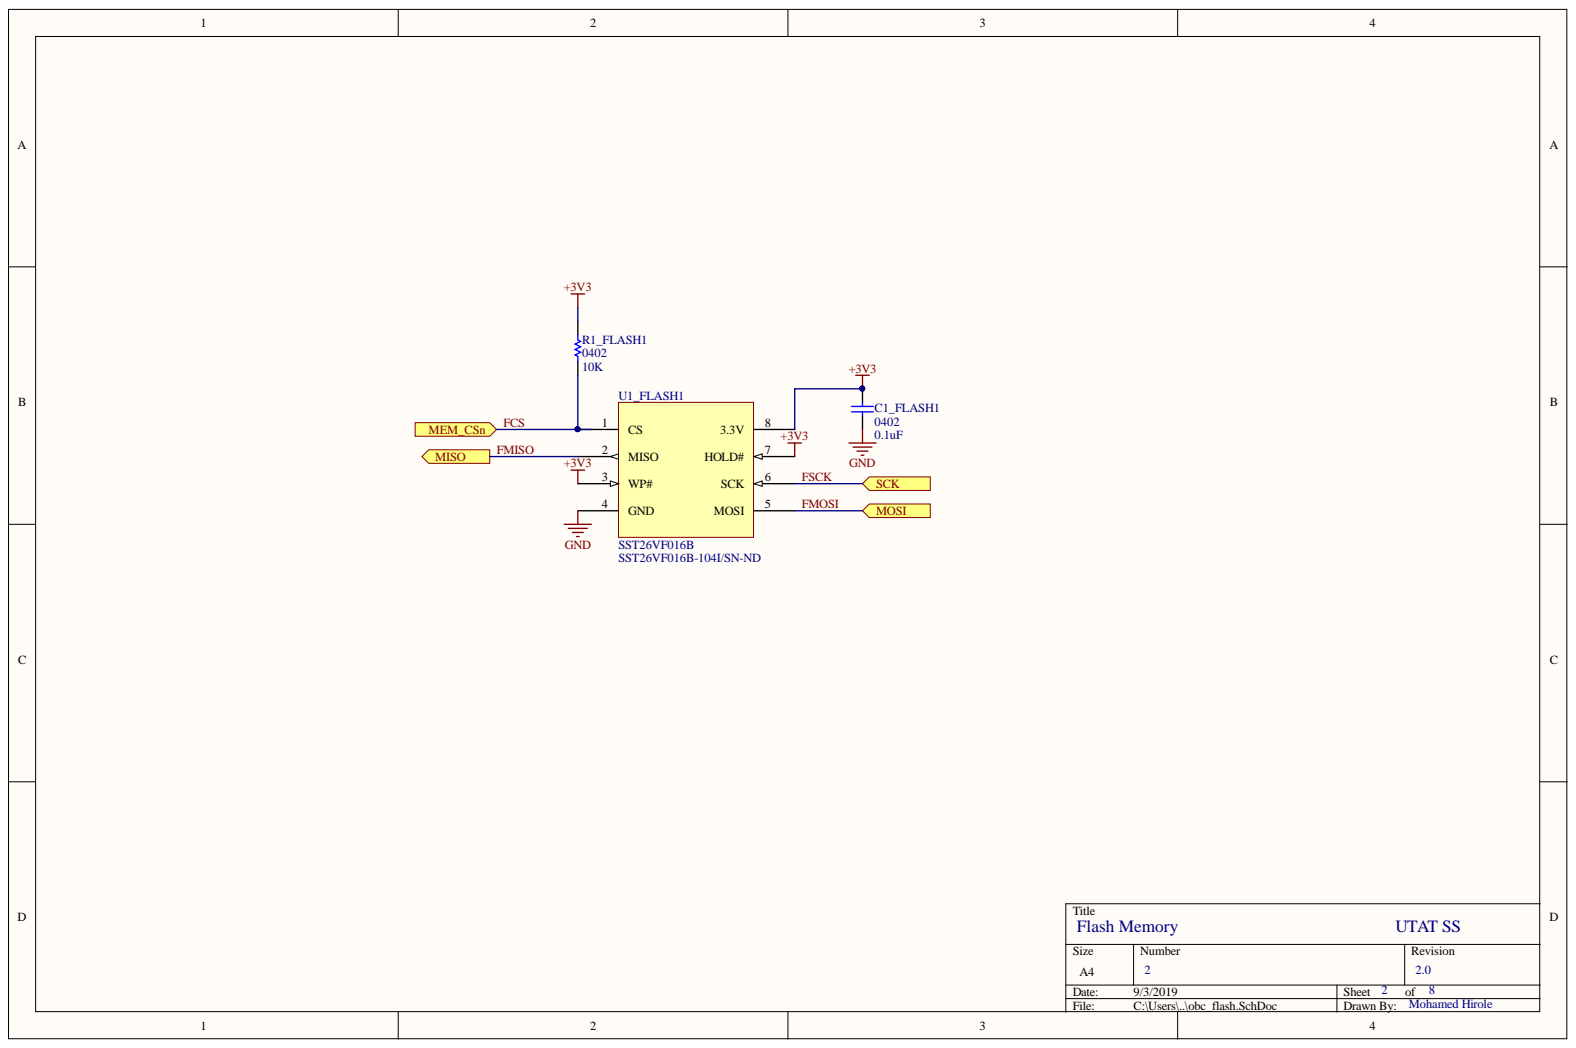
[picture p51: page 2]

Size A4 | Number 2 | Revision 2.0

Date: 9/3/2019 | Sheet 2 of 8
File: C:\Users\..\obc_flash.SchDoc | Drawn By: Mohamed Hirole

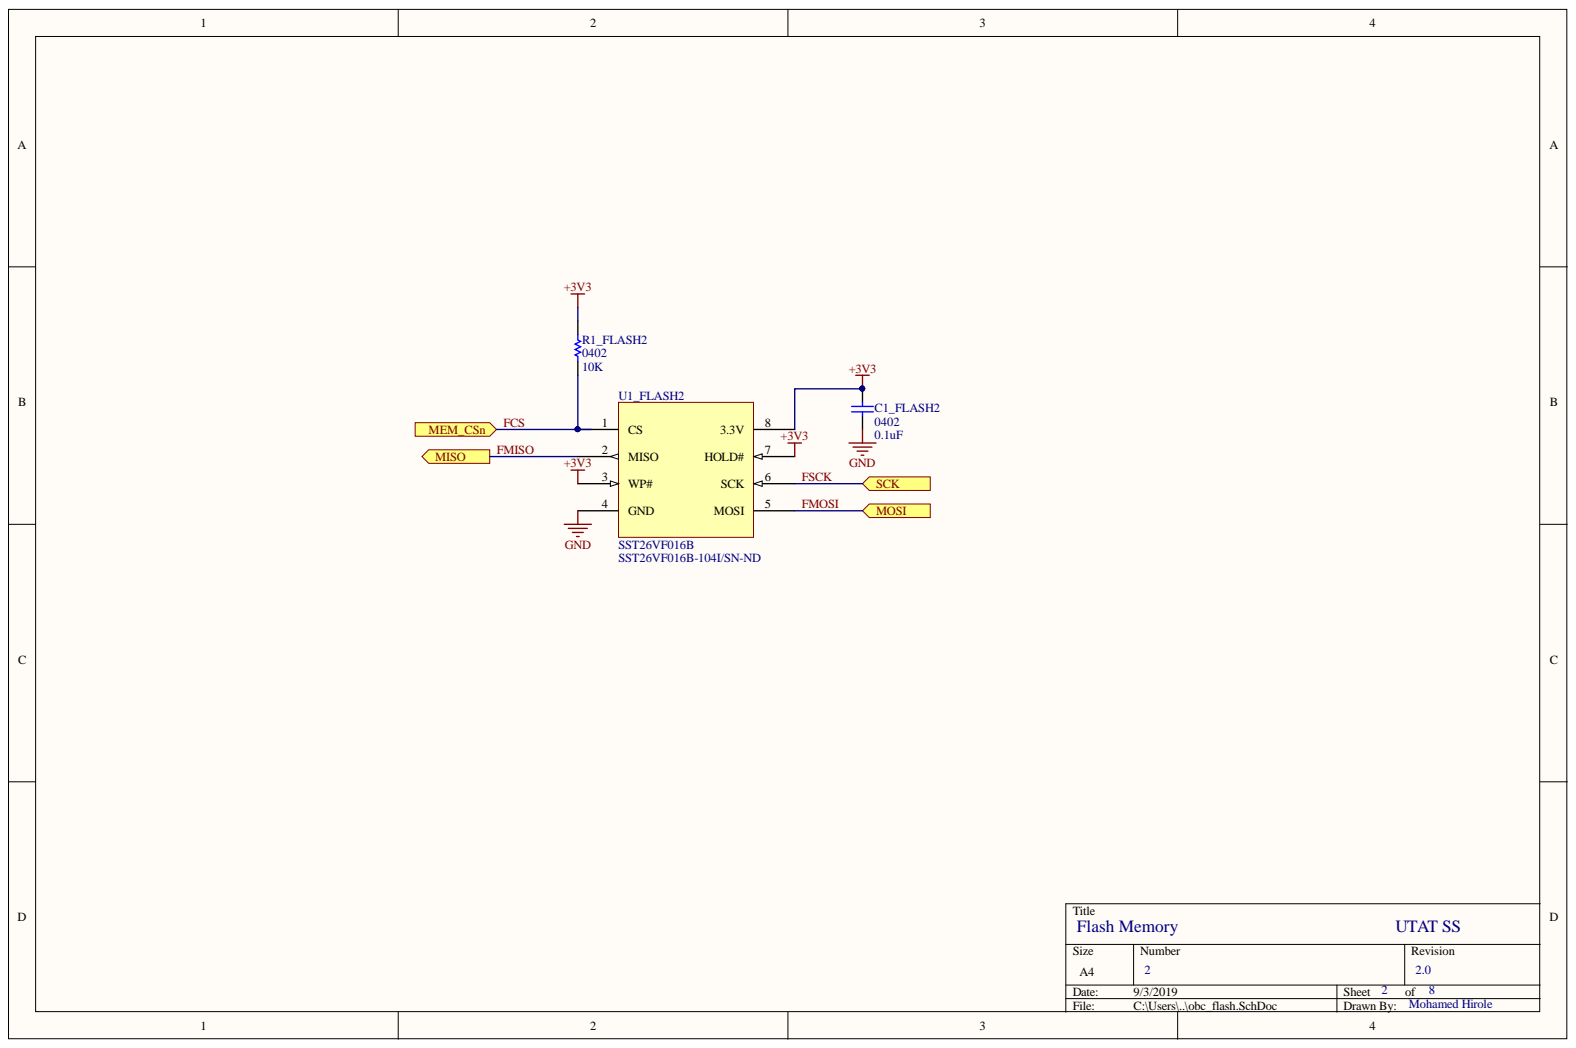
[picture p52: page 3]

Size A4 | Number 2 | Revision 2.0

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

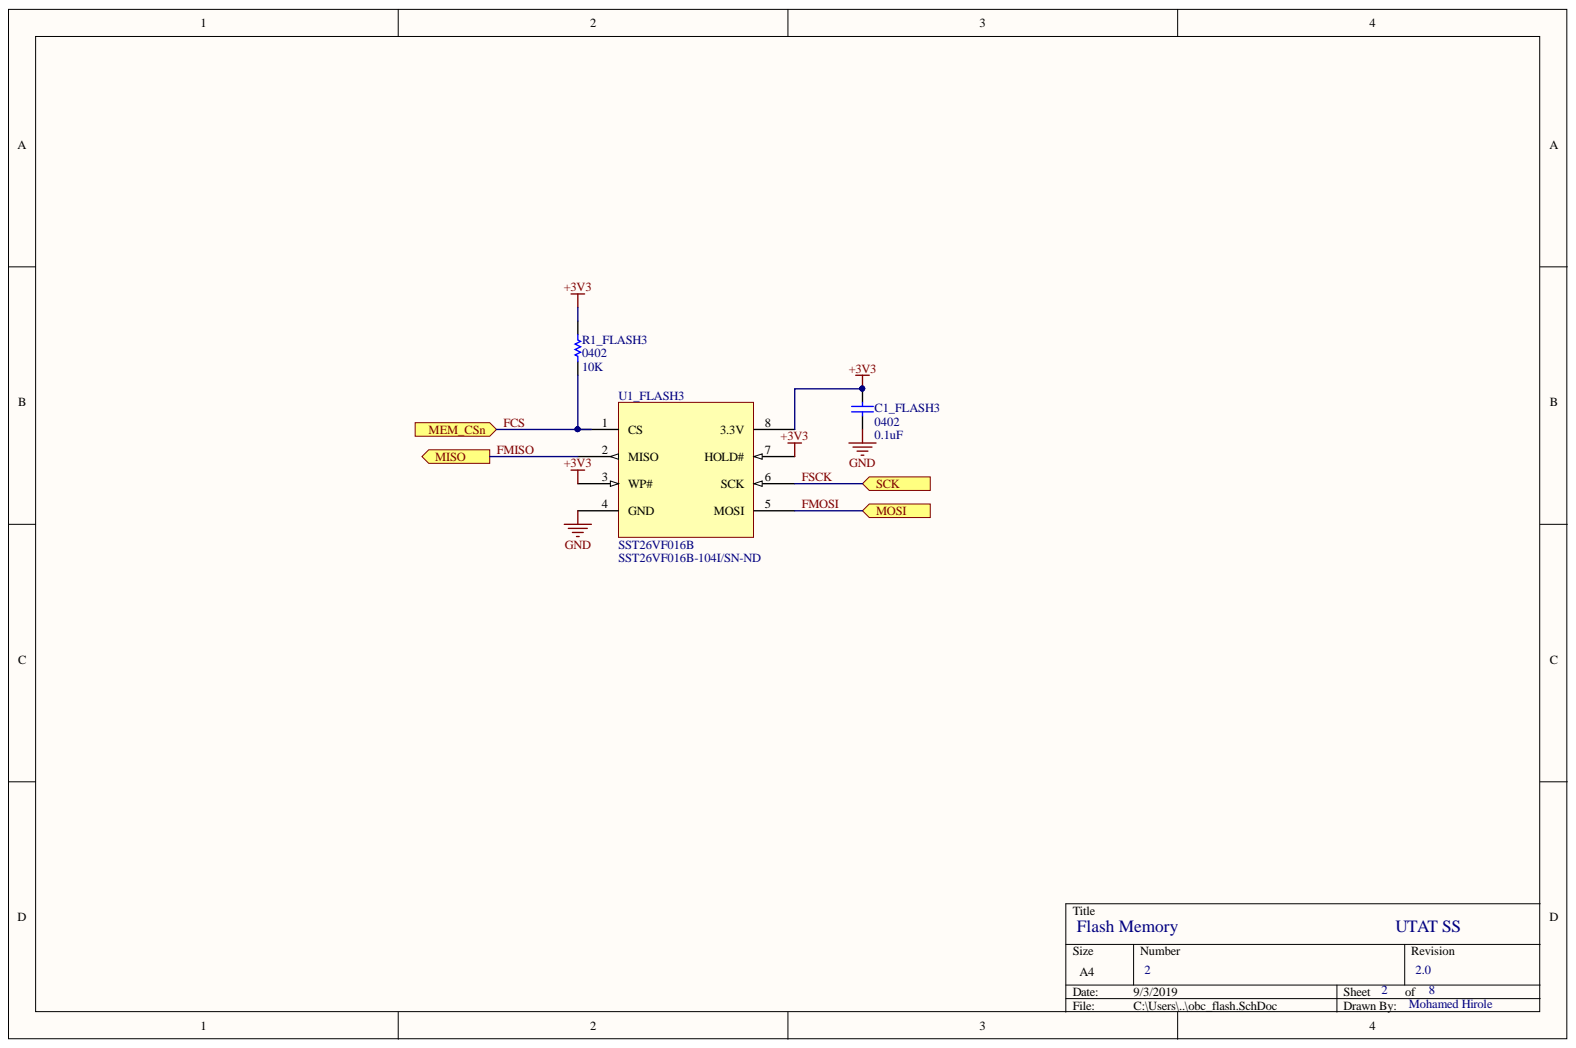
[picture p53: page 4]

Size A4 | Number 2 | Revision 2.0

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

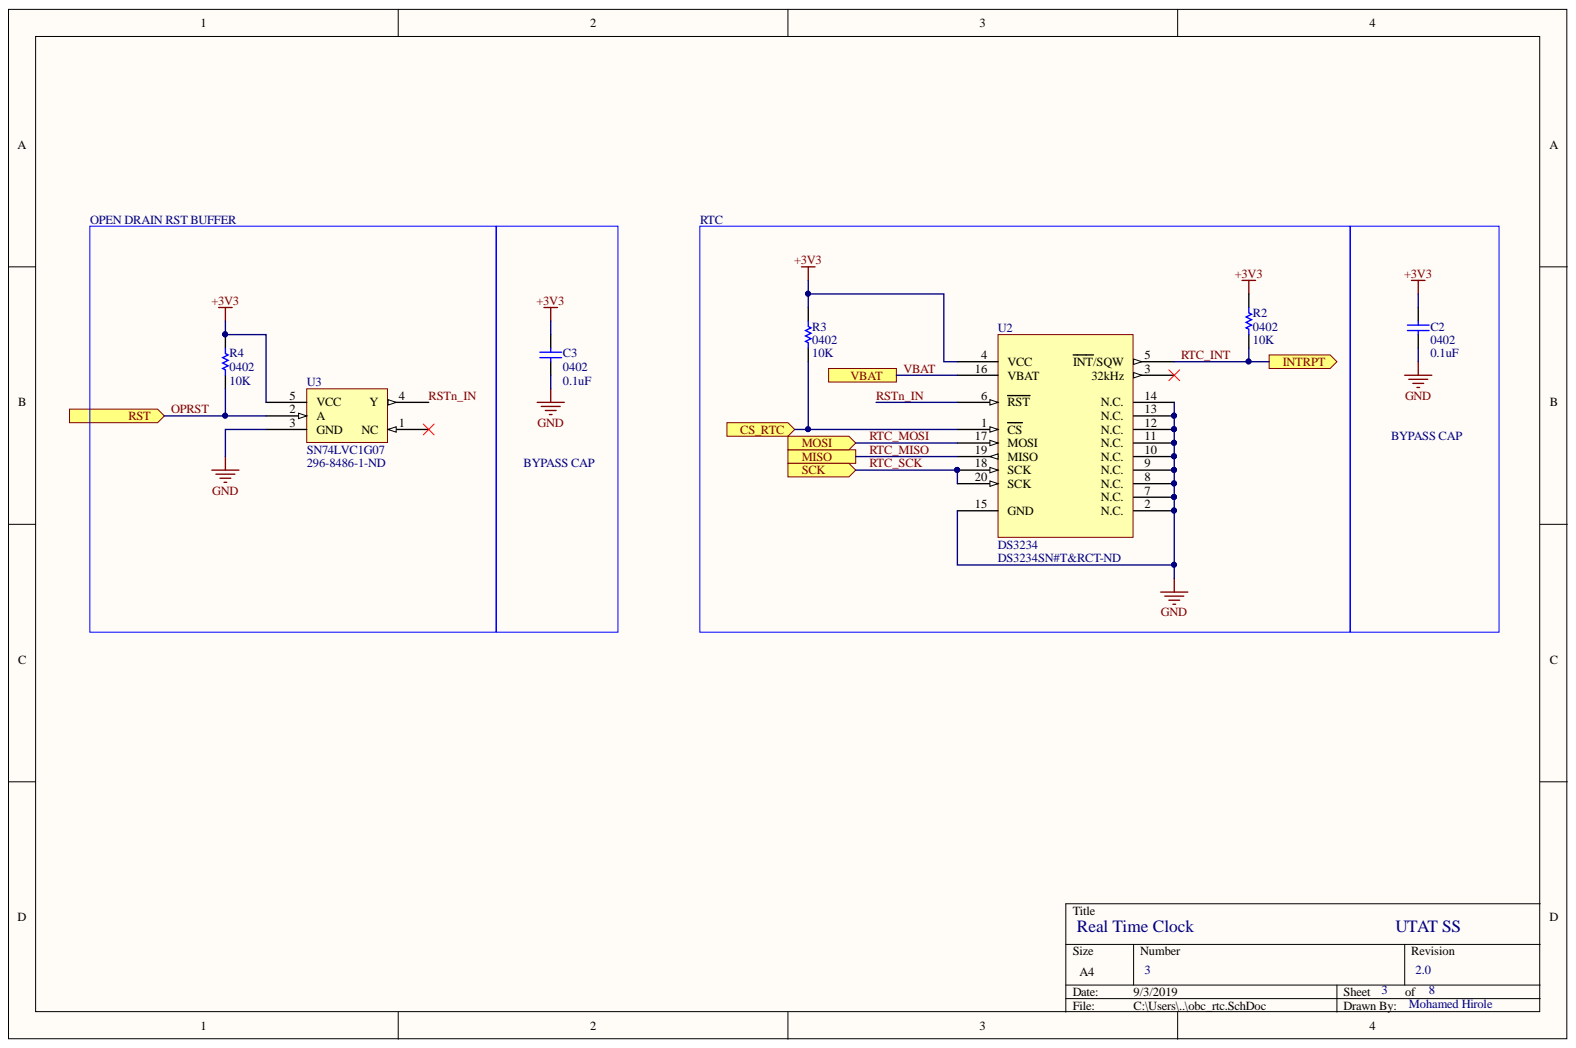
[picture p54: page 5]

Numbe r | R evision 0

: 9/3/2019 | She et 3 of 8
File : C:\Use rs\. .\obc_rtc . S chDoc | D r a wn By: Mohamed Hirole

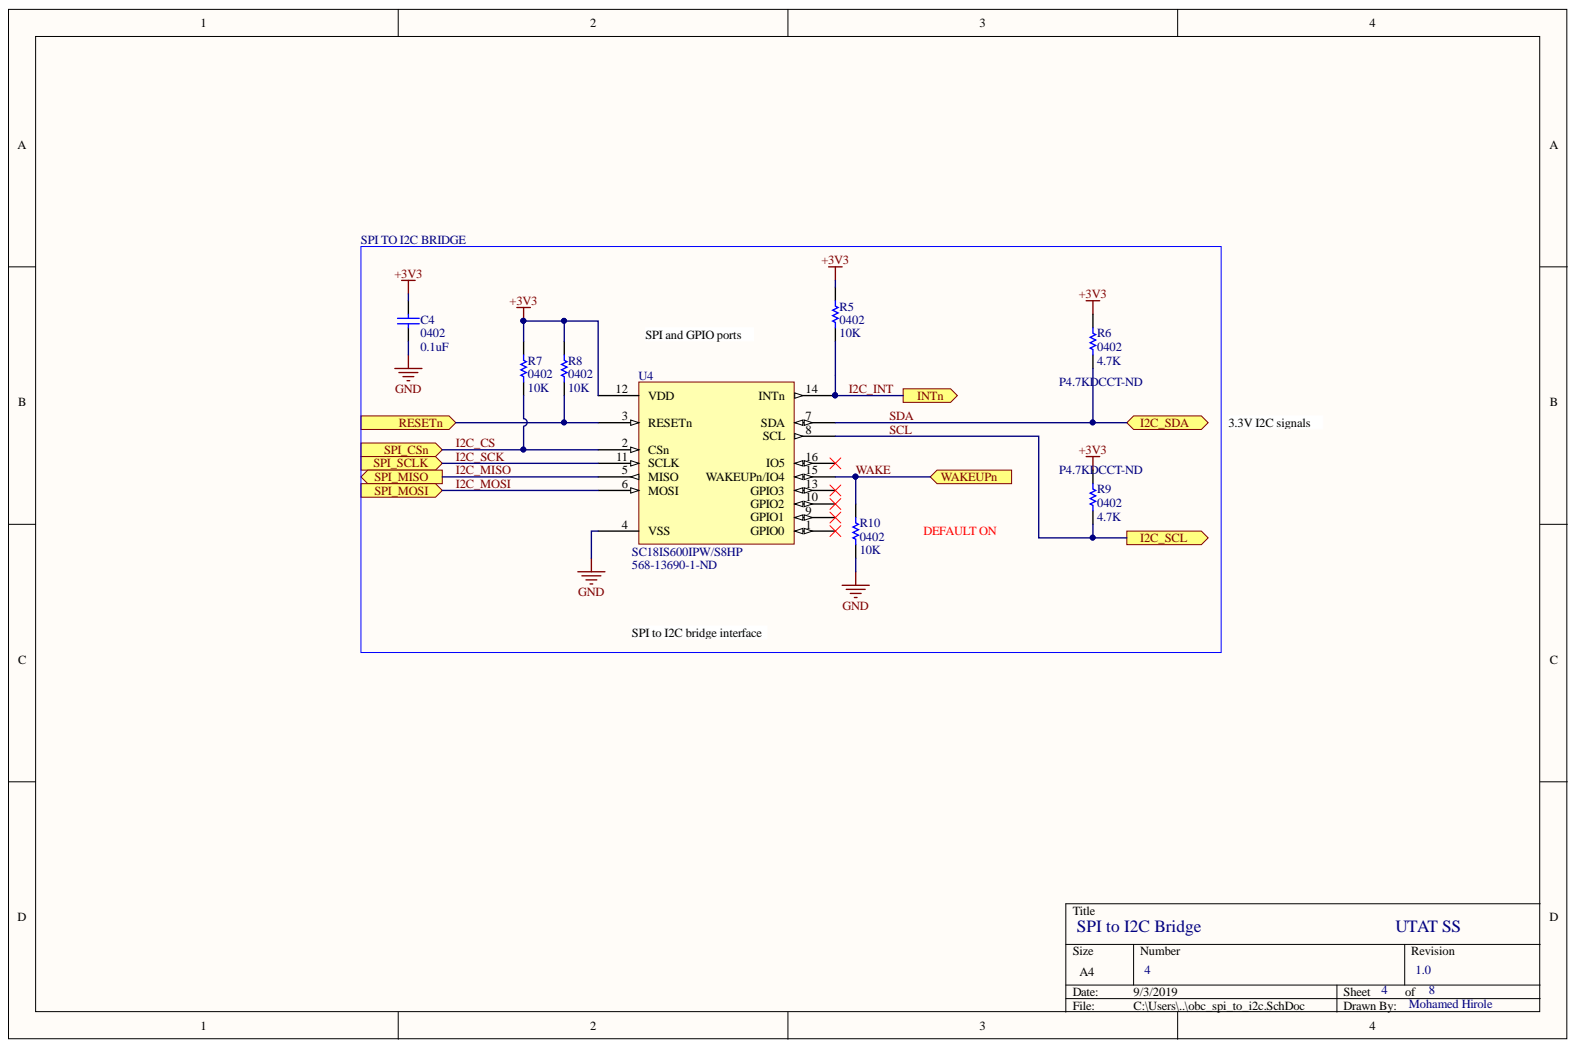
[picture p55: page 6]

Numbe r | R evision 0

: 9/3/2019 | She et 4 of 8
File : C:\Use rs\. .\obc_spi_to_i2c . S chDoc | D r a wn By: Mohamed Hirole

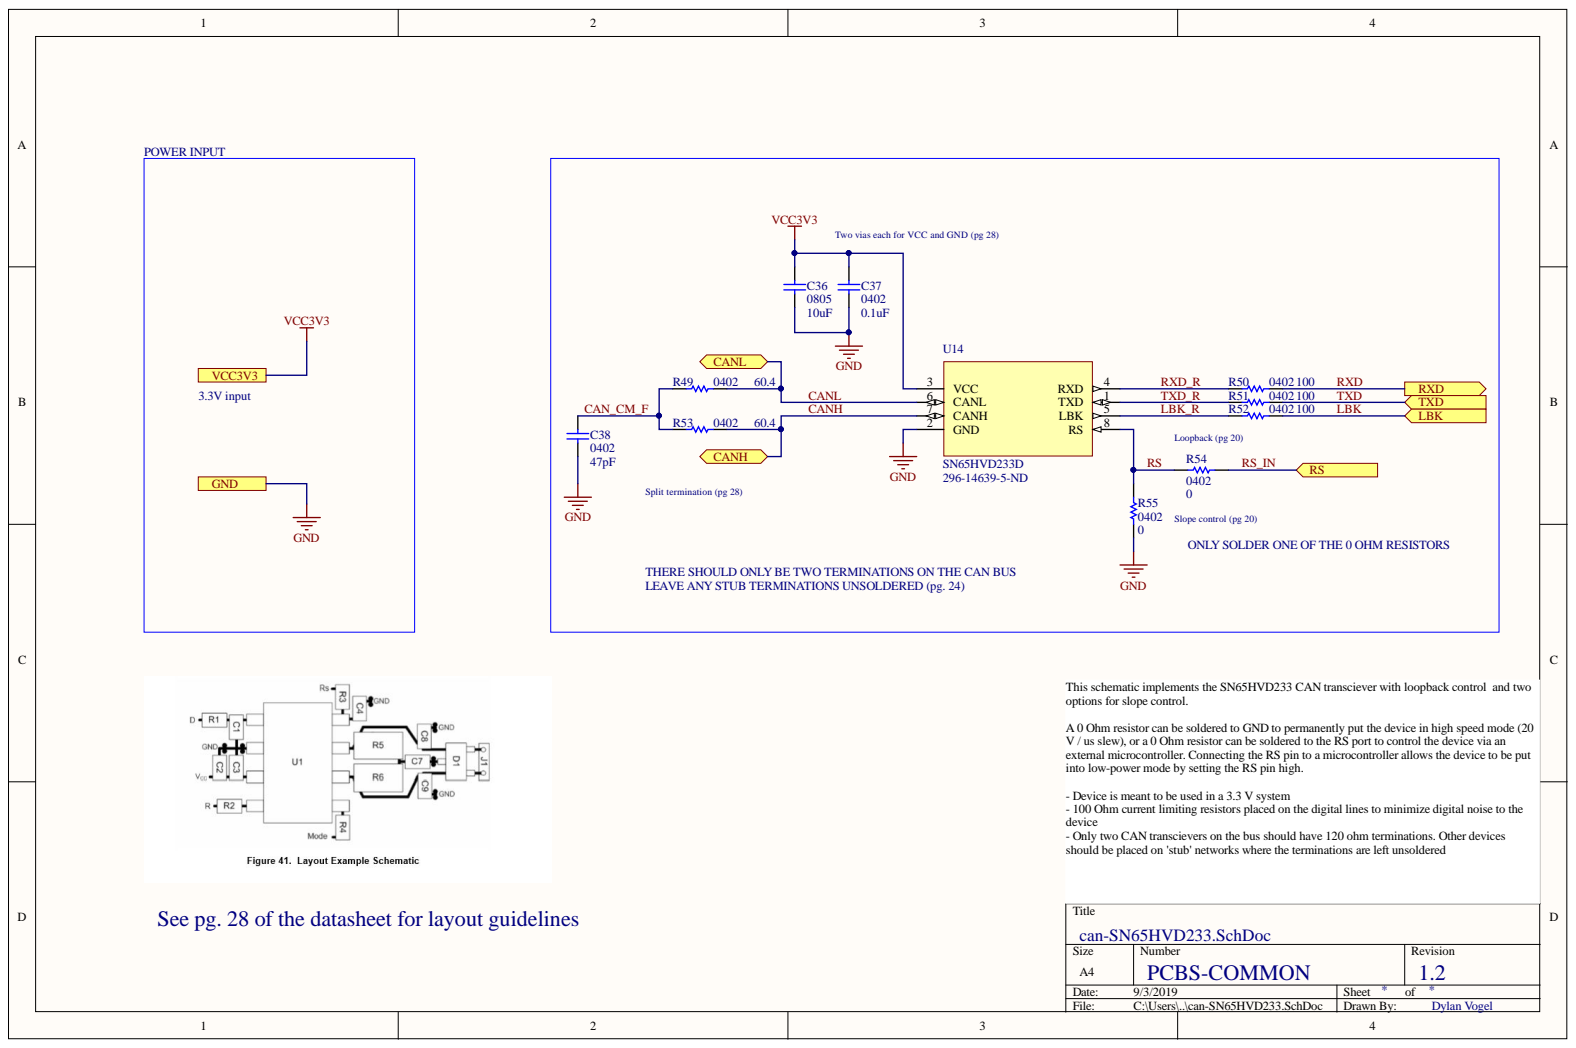
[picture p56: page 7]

Two vias each for V

This schematic implements the
options

rmanently put the devic
red to the
S pin high.

r mode by setting the

ant to be used in

ed on the digital lines to minimiz

e digital noise to the

rs on the bus should have 120 ohm te

Numbe r PCBS-COMMON | R evision 1. 2

: 9/3/2019 | She et * of *Dylan
File : C:\Use rs\. .\c an-S N65H V D233. S chDoc | D r a wn By: Voge l

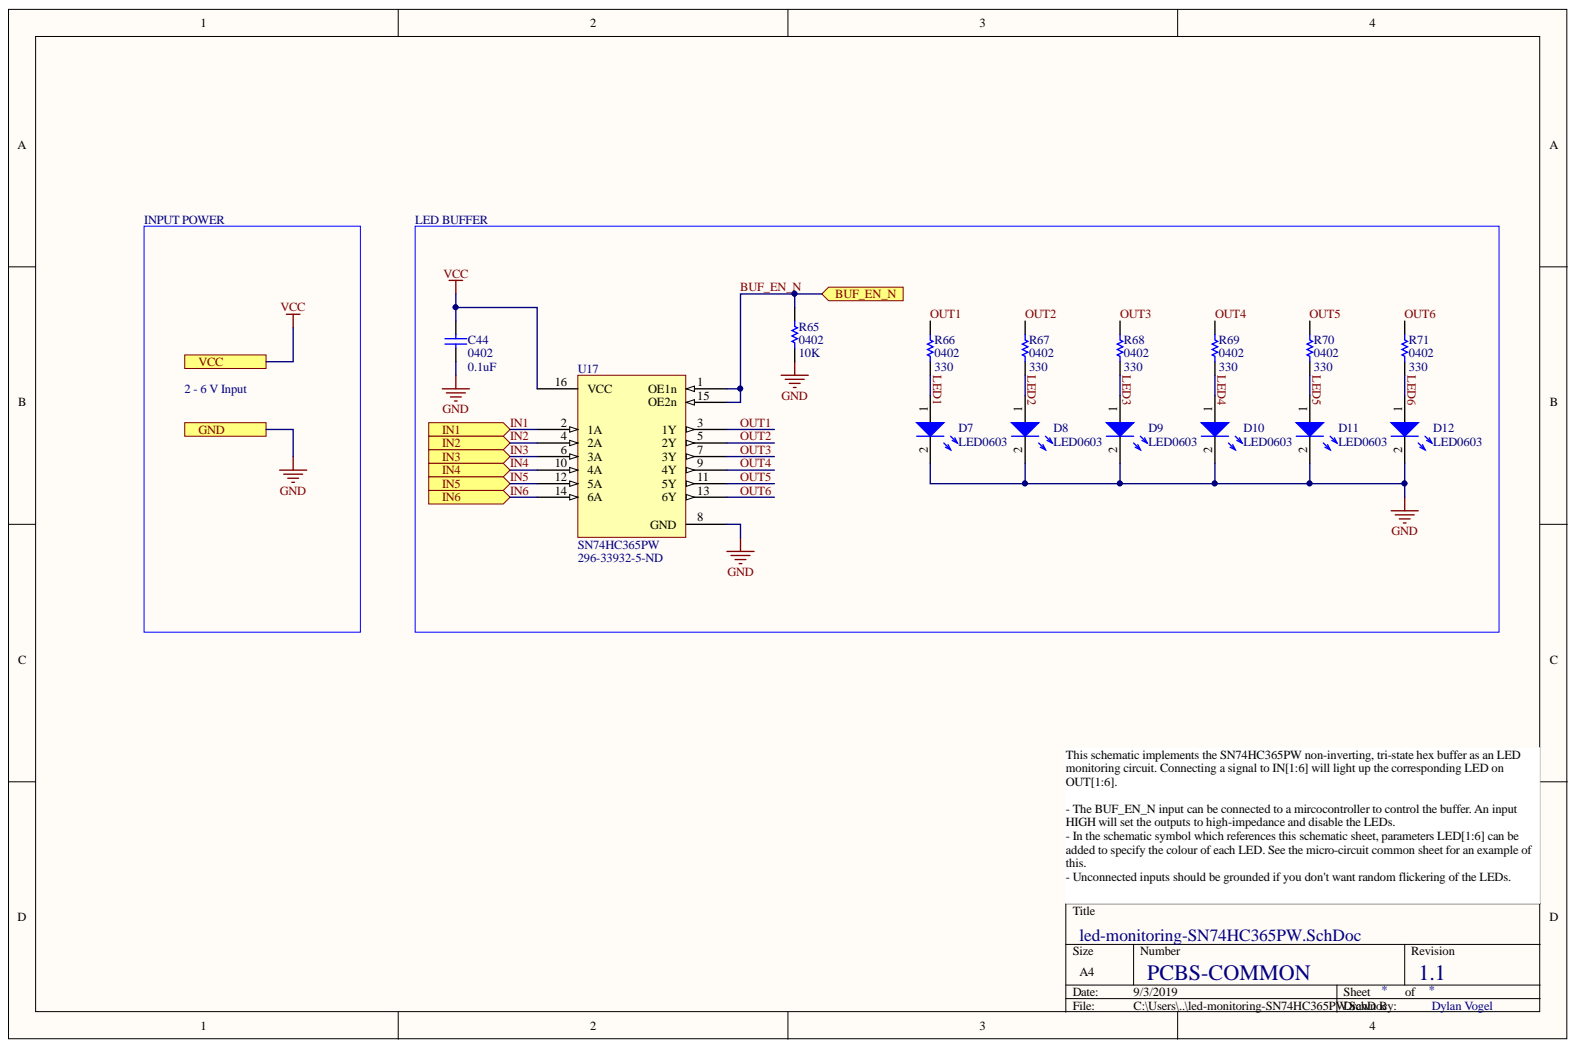
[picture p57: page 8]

rting, tri-state hex buffe

will light up the

a mir
and disable the LEDs.

will set the outputs to high-impedanc

cted inputs should be grounded if you don't
Title Size
led-monitoring-SN74HC365PW.SchDoc

ring of the LEDs.

Numbe r PCBS-COMMON | R evision 1. 1

: 9/3/2019 | She et * of *Dylan
File : C:\Use rs\. .\led-monitoring-S N74H C365P | WD.SrcahDwn ocBy: Voge l

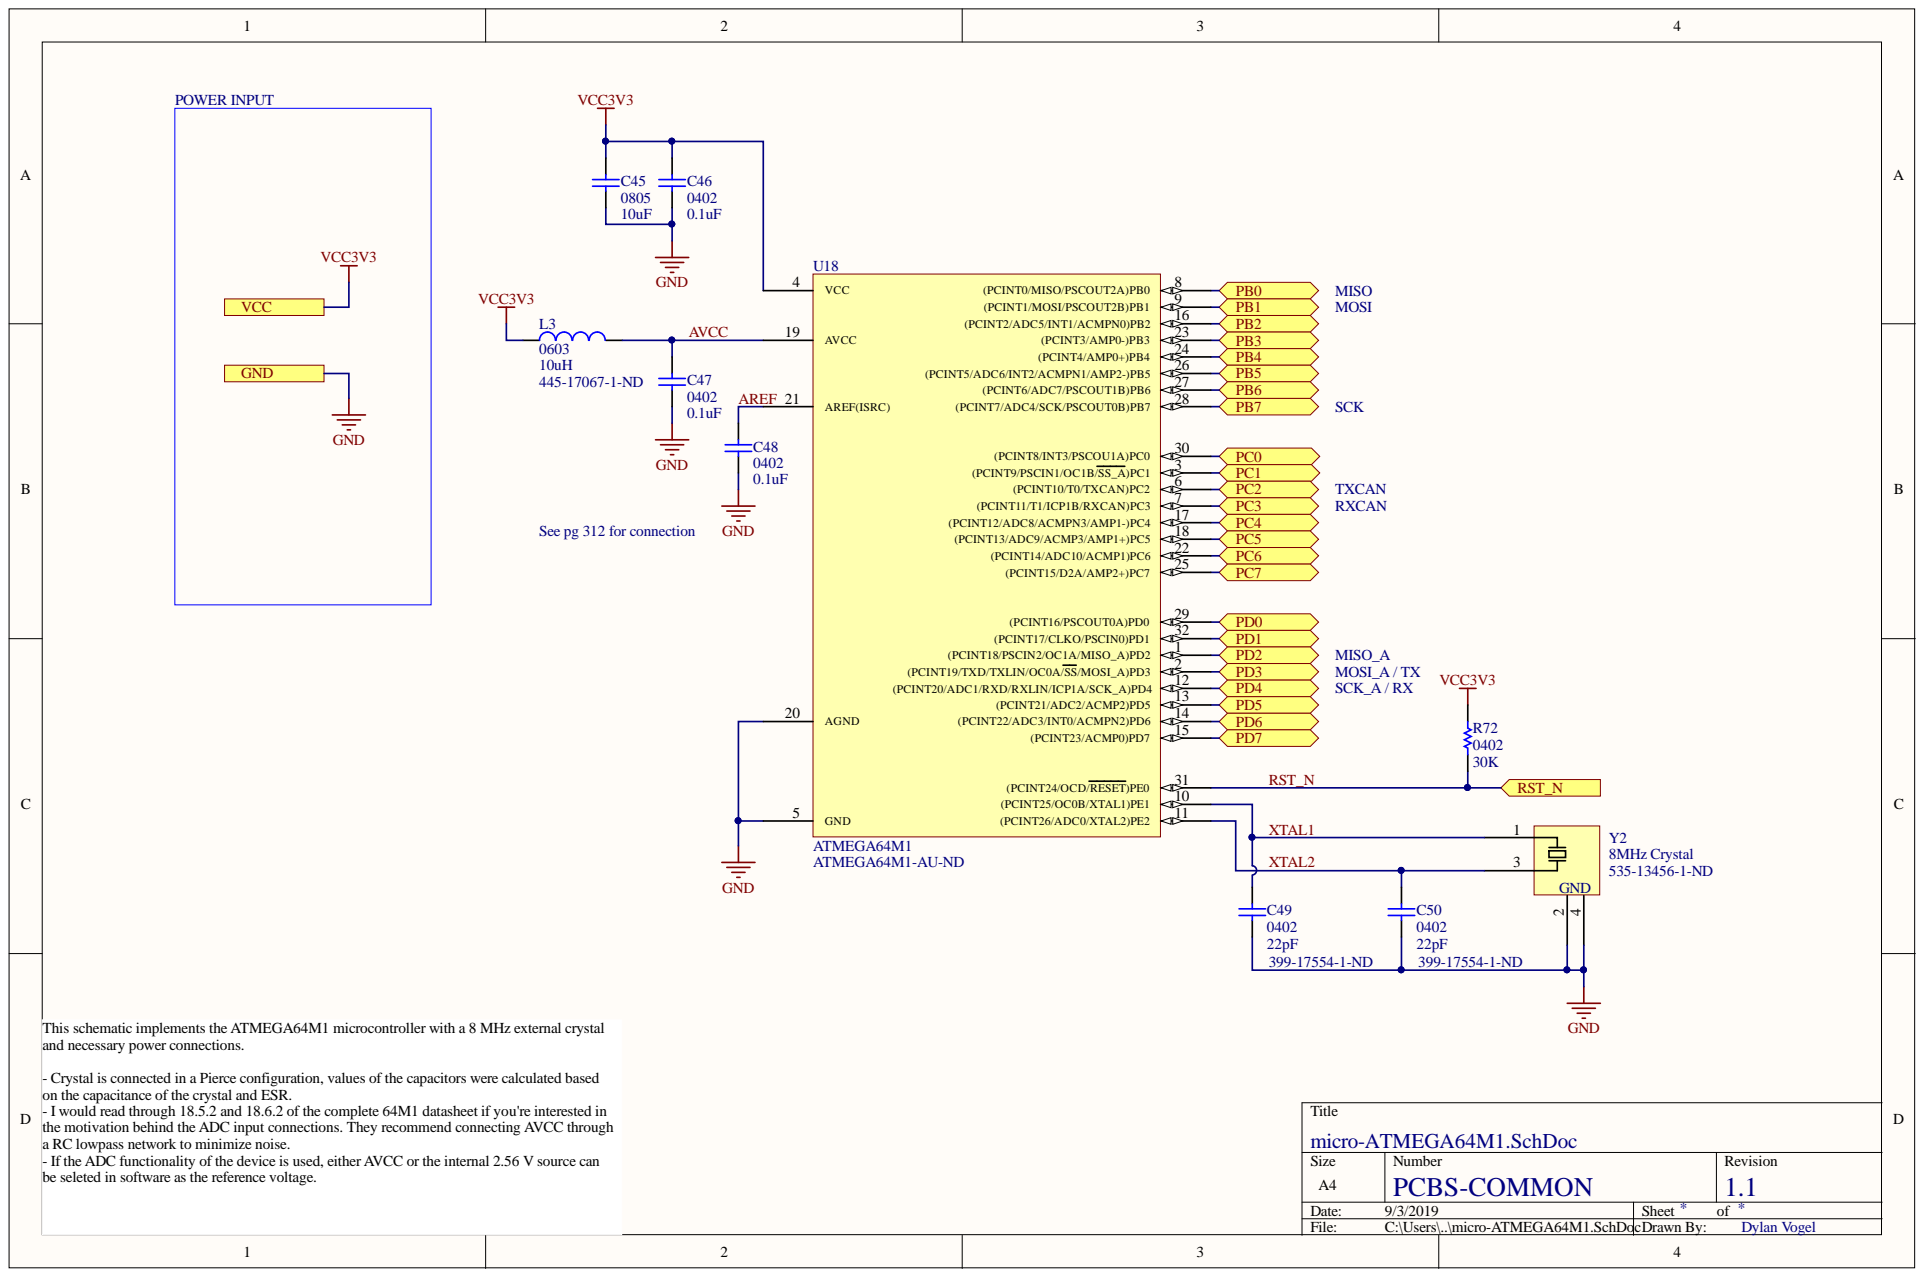
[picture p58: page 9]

This schematic implements the
and ne

C lowpass network to minimiz
f the

functionality of the devic
are

Numbe r PCBS-COMMON | R evision 1. 1

: 9/3/2019 | She et * of *Dylan
File : C:\Use rs\. .\mic ro-ATMEG A64M1. S chDoc | D r a wn By: Voge l

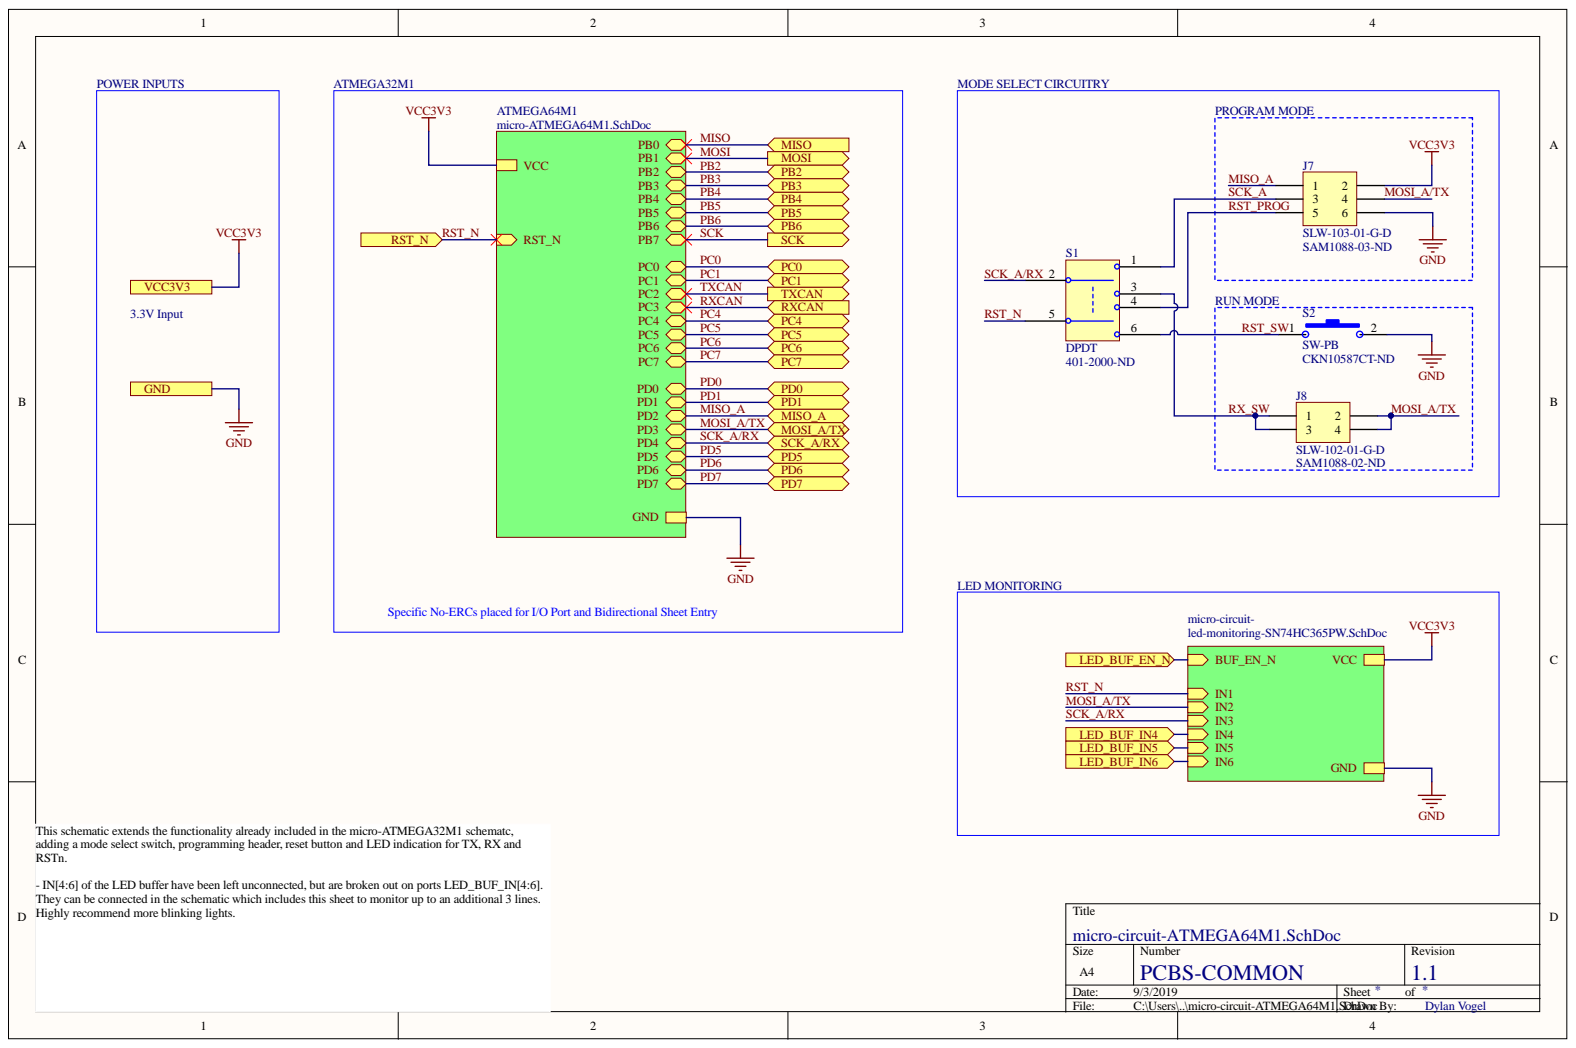
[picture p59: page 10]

ady included in the mic

[4:6] of the LED buffe

which includes this she

are broken out on ports LED_B
et to monitor up to

cted in the schematic
e blinking lights.

Numbe r PCBS-COMMON | R evision 1. 1

: 9/3/2019 | She et * of *Dylan
File : C:\Use rs\. .\mic ro-cir cuit-ATMEG A64M1. | SDchDrawocn By: Voge l

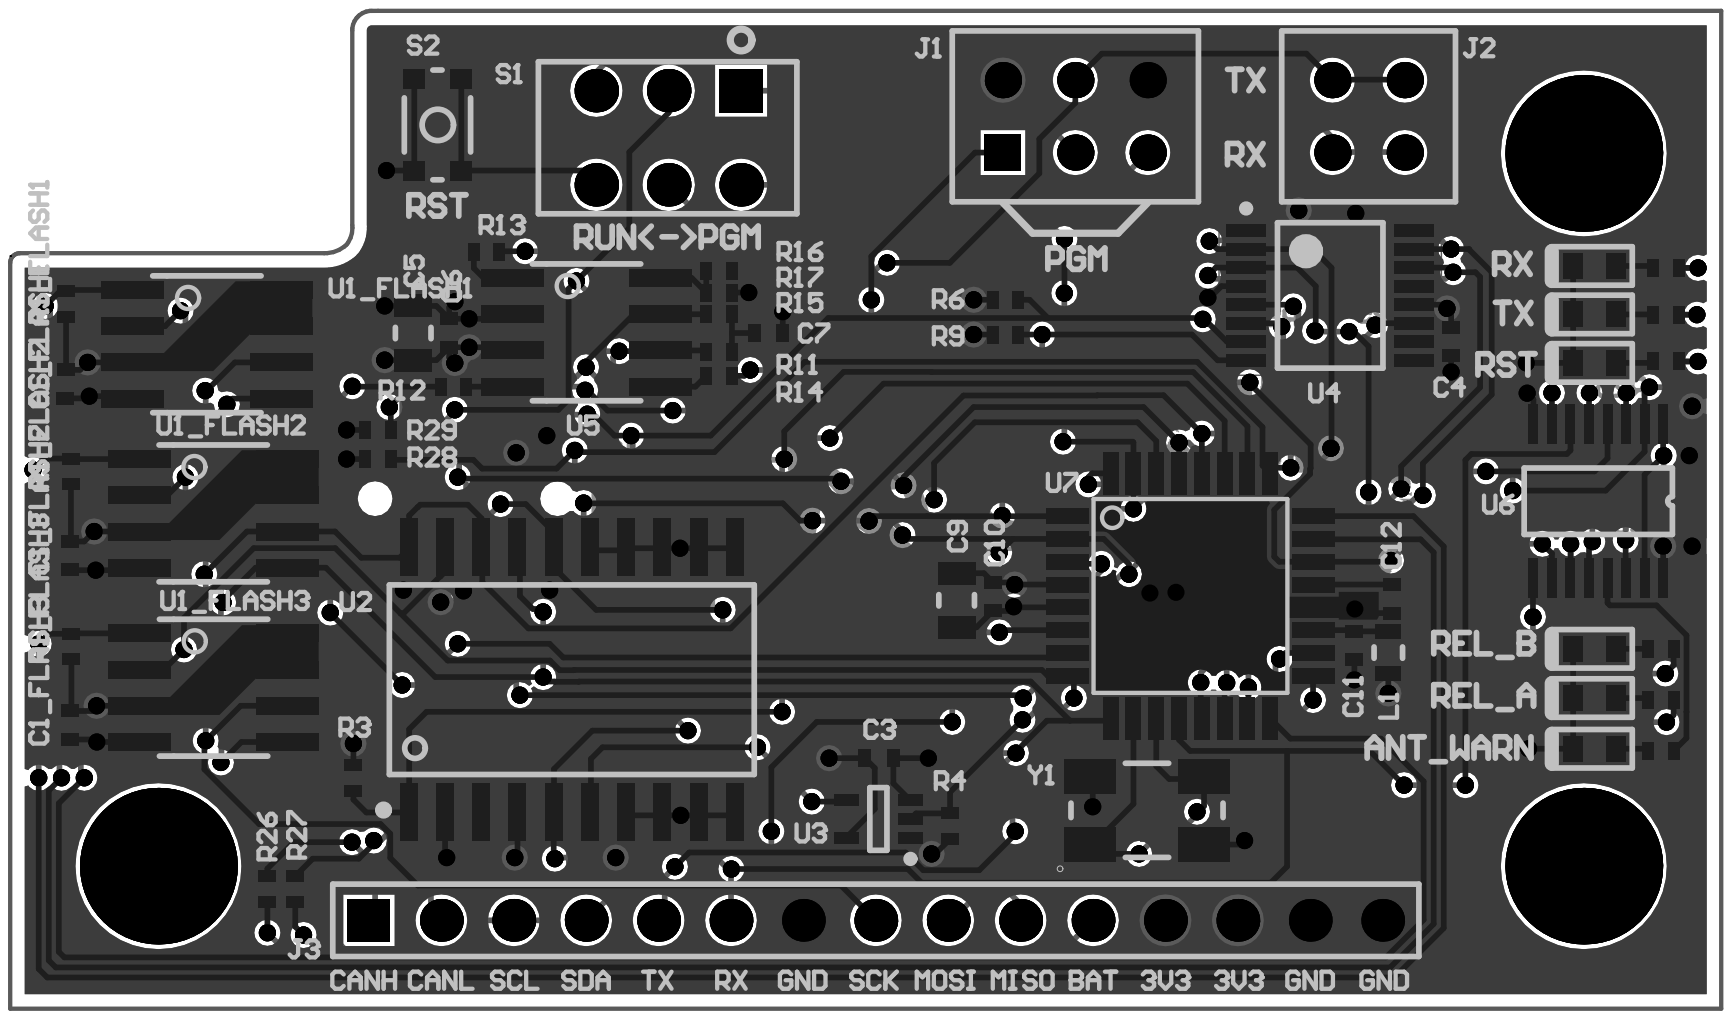
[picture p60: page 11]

# Board Stack Report

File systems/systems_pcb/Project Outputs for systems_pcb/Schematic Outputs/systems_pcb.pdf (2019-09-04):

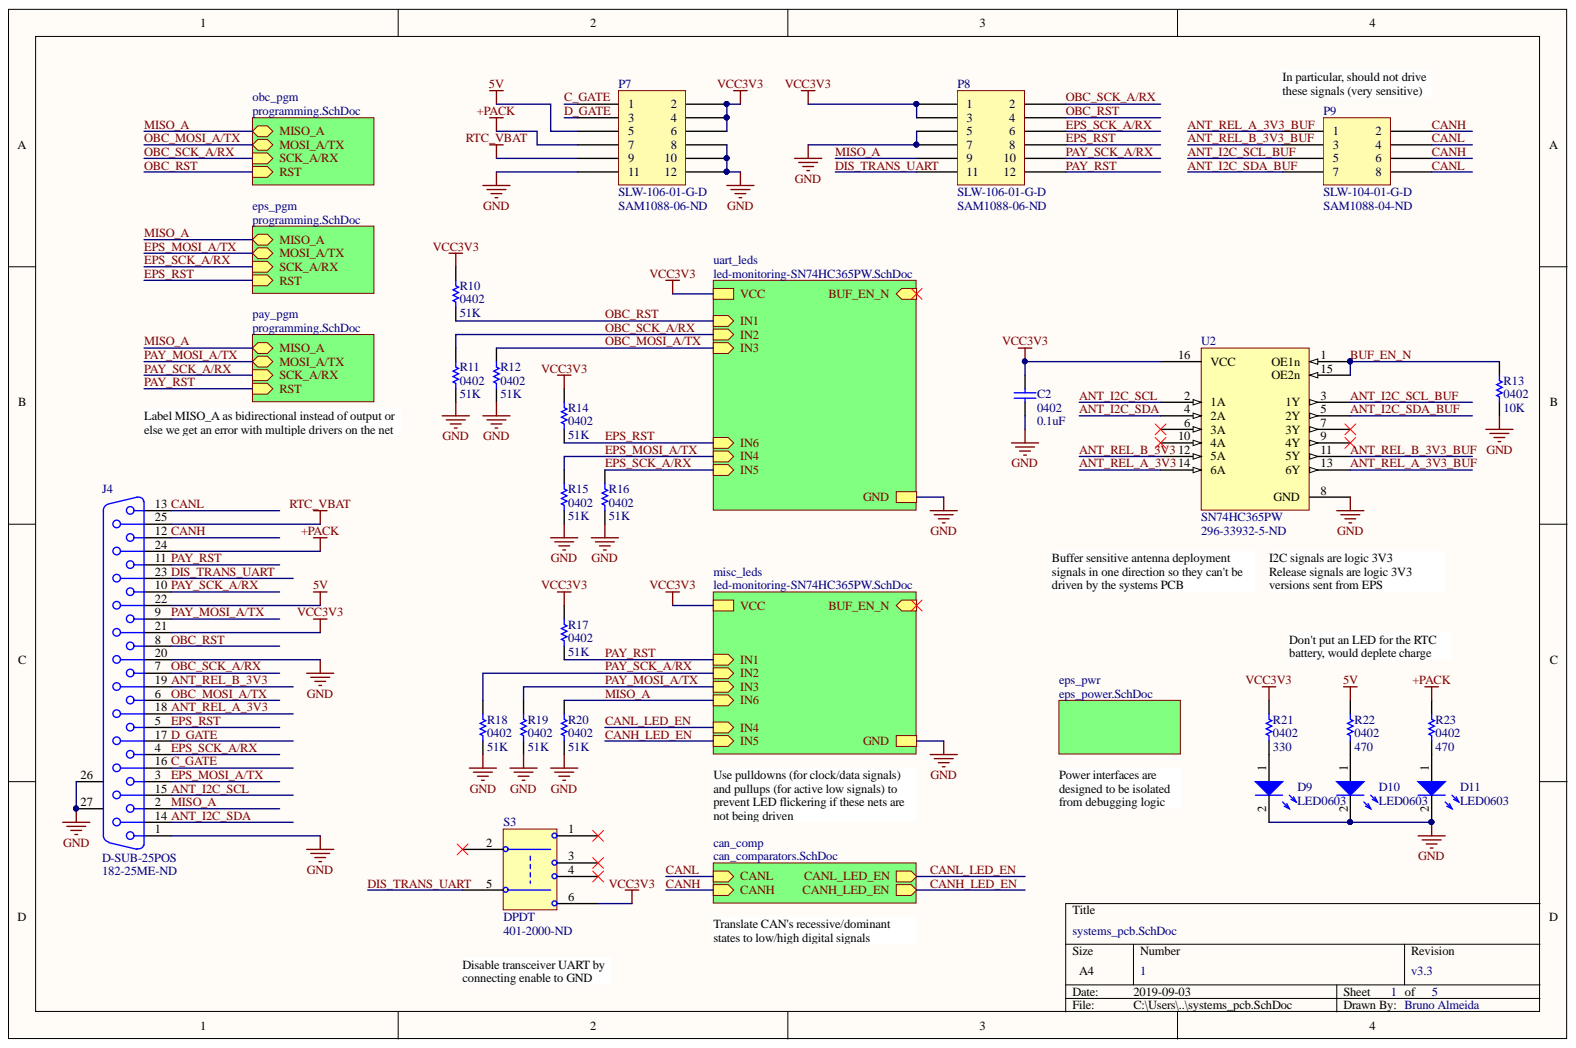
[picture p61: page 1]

In particular, should not drive
these signals (very sensitive)

Label MISO_A as bidirectional instead of output or
else we get an error with multiple drivers on the net

Buffer sensitive antenna deployment
signals in one direction so they can't be
driven by the systems PCB

I2C signals are logic 3V3
Release signals are logic 3V3
versions sent from EPS

Don't put an LED for the RTC
battery, would deplete charge

Use pulldowns (for clock/data signals)
and pullups (for active low signals) to
prevent LED flickering if these nets are
not being driven

Power interfaces are
designed to be isolated
from debugging logic

Translate CAN's recessive/dominant
states to low/high digital signals

Disable transceiver UART by
connecting enable to GND

Size A4 | Number 1 | Revision v3.3

Date: 2019-09-03 | Sheet 1 of 5
File: C:\Users\..\systems_pcb.SchDoc | Drawn By: Bruno Almeida


ators have open-dr

Numbe r 2 | R evision v3. 3

: 2019-09-03 | She et 2 of 5
File : C:\Use rs\. .\c an_compar ators. S chDoc | D r a wn By: B runo Almeida


OLA
691102710002 SOLAR POWER Screw terminal to sc

Should not unify the grounds he

On the EP
betw
to the deployment switch state

Numbe r | R evision 3

: 2019-09-03 | She et 3 of 5
File : C:\Use rs\. .\eps_pow e r . S chDoc | D r a wn By: B runo Almeida


rting, tri-state hex buffe

will light up the

a mir
and disable the LEDs.

will set the outputs to high-impedanc

cted inputs should be grounded if you don't
Title Size
led-monitoring-SN74HC365PW.SchDoc

ring of the LEDs.

Numbe r PCBS-COMMON | R evision 1. 1

: 2019-09-03 | She et 4 of 5Dylan
File : C:\Use rs\. .\led-monitoring-S N74H C365P | WD.SrcahDwn ocBy: Voge l


Size A4 | Number 5 | Revision v3.3

Date: 2019-09-03 | Sheet 5 of 5
File: C:\Users\..\programming.SchDoc | Drawn By: Bruno Almeida


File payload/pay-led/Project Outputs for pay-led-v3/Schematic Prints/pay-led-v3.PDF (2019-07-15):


Optional input filtering for SI



A 1 1 2 | | 2 7
A 2 1 3 | | 2 6


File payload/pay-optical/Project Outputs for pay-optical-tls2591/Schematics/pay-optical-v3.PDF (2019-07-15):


VCC_SENSE | | MUX1_RST_N

CURR_MON_OUT VCC3V3_S_EN | CURR_SENSE | | MUX2_RST_N



EMERGENCY "I DON'T WANT ANY OF THIS NEWFANGLED SWITCH NONSENSE" SHUNT




SDA1 | LED2

SCL2 SDA2

SCL3 SDA3

SCL4 SDA4

SCL5 SDA5

SCL6 SDA6

SCL7 SDA7

SDA8



heet for an examp

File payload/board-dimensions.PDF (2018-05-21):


UNLESS OTHERWISE SPECIFIED: | | NAME | DATE
DIMENSIONS ARE IN INCHES TOLERANCES: FRACTIONAL ANGULAR: MACH BEND TWO PLACE DECIMAL THREE PLACE DECIMAL | DRAWN

CHECKED | | | TITLE:

ENG APPR.
MFG APPR.

INTERPRET GEOMETRIC TOLERANCING PER: | Q.A.
MATERIAL | | SIZE A | DWG. NO. pcb1-jig | REV

PROPRIETARY AND CONFIDENTIAL
THE INFORMATION CONTAINED IN THIS
DRAWING IS THE SOLE PROPERTY OF
<INSERT COMPANY NAME HERE>. ANY
REPRODUCTION IN PART OR AS A WHOLE
WITHOUT THE WRITTEN PERMISSION OF
<INSERT COMPANY NAME HERE> IS
PROHIBITED.

NEXT ASSY | USED ON | FINISH

APPLICATION | DO NOT SCALE DRAWING | | SCALE: 1:2 | WEIGHT: | SHEET 1 OF 1

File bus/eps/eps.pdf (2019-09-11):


Systems PCB DSUB Connector

LED must be placed
near the edge of the
board by the DSUB
cutout

Converter Output Screw Terminals


Size A | Number 2 | Revision 1.0

File: C:\Users\..\eps.SchDoc | Drawn By:


g (to be able to

VC C _ BOOST 1 | | 4
COMP | 2 | | 5

ILIM_ PAY | 1 9 | | 7

SS | 1 0 | | 3 | FSW

Size A | Nu m ber | Revisio n 2.0

Date: --1 | Sheet o f
File: C:\Users\..\b o ost.SchDo c | Drawn B y : J. Reimer T. Yeu n g M. Au


Need to label which FET is which (charge or discharge)
for the batt pro circuit on the PCB.

Positive terminal --> +DEP --> filter
Negative terminal --> -DEP --> RBF --> GND

Load switch: convention for VIN and VOUT is assuming discharge: VOUT points toward the load

D_GATE | C_GATE

BATT PRO FET UNITY GAIN BUFFERS


5 | 1 3
6 | 1 4


GND 296-24251-1-ND I_X-_R


Some 100 ohm current limiting
resistors needed here?

The DAC and HEATER lineup needs to be cleaned up to make room for the PEX: the
flow/readability of this schematic could be improved

INTA and INTB are interrupts that can
be connected to 64M1


1 1 1 | NRST ABS0 7 | -C 3 4

Size A | Nu m ber | Revisio n 1.0

File: C:\Users\..\eps_im u.SchDo c | Drawn B y J. Reimer T. Yeu n


8 of the datasheet for lay


RST _SW | S2 1 2 CK N 1 0 5 8

hey can be co

uffer have been left u
he schemat



VCC

ders can be co


heet for an examp



2 2
3 3


5 | TRIM/ N R


ILIM | 8

L DST RT | 1 2

1 4 | 1 | V d t
2 6 | 7 | ITIME



Questions:
- I think these deploymeny switches are bidirectional: in the
current setup, VIN and VOUT are configured in the direction of
battery discharge. Is there a reason either of these should be
switched around?
- Is there an optimal value for the pull-downs? I put them at 50K
because they will have BATT voltage driving the load switches
high for the entire satellite lifetime so increased it, but still pretty
arbitrary at 50K

Convention for VIN and VOUT is assuming discharge: VOUT points toward the load

All ON-state pull-downs are 50K to avoid drawing too much current


Input to output capacitor ratio should be 10:1

VIN 9 VIN 2 VIN 1

VBIAS 3


Designed for +5V, see note below

Non-Inverting Open Drain Comparator
IF IN+ > IN-, OUT = Z, HEATER ON
IF IN+ < IN-, OUT = LOW, HEATER OFF

LED HEATER STATUS INDICATION

Might need to be changed based on your AVCC level. Designed for 5V

This schematic implements a single heater control circuit, relying on an open-drain comparator and
NMOS switch for completely analog operation.

The temperature setpoint is set via the voltage on the TEMP_VREF pin, which is compared against the
voltage on the TEMP_VIN pin. If the voltage on TEMP_VREF is higher, the output of the comparator
will go high-impedance and drive the gate of the NMOS to 5V through the 1K pull-up resistor. This
should be enough to switch the MOSFET in triode with a relitively low VDS at our target current

Conversely, when TEMP_VIN is above TEMP_VREF, the output is switched to GND and the MOSFET
turns off. How you decide to set TEMP_VREF and TEMP_VIN is entirely up to you.

The circuit is designed to work at 5V. To operate at different voltages, just be sure to check the relevant
ratings on the different components.


HEATER CONTROL 1
heater-control-comparator.SchDoc

+3V3 heater-control-comparator.SchDoc

Voltage divider between thermistor (DF13 connector)
and 10K 0402 on PCB.

On-PCB thermistors for hot-spot temperature sensing.


Cannot open file C:\Users\Jaden Reimer\Desktop\enduro.PNG

Cannot open file C:\Users\Jaden Reimer\Desktop\H1.PNG

TRANS_RxD
Cannot open file C:\Users\Jaden Reimer\Desktop\H2.PNG TRANS_TxD



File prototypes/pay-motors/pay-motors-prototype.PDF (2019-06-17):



VCP 3 | | BVREF

C13_DRV8843N1 | 0603 1M | C11_DRV8843N1 | | CP1 1


VCP 3 | | BVREF

C13_DRV8843N2 | 0603 1M | C11_DRV8843N2 | | CP1 1


heet for an examp



hey can be co

uffer have been left u
he schemat




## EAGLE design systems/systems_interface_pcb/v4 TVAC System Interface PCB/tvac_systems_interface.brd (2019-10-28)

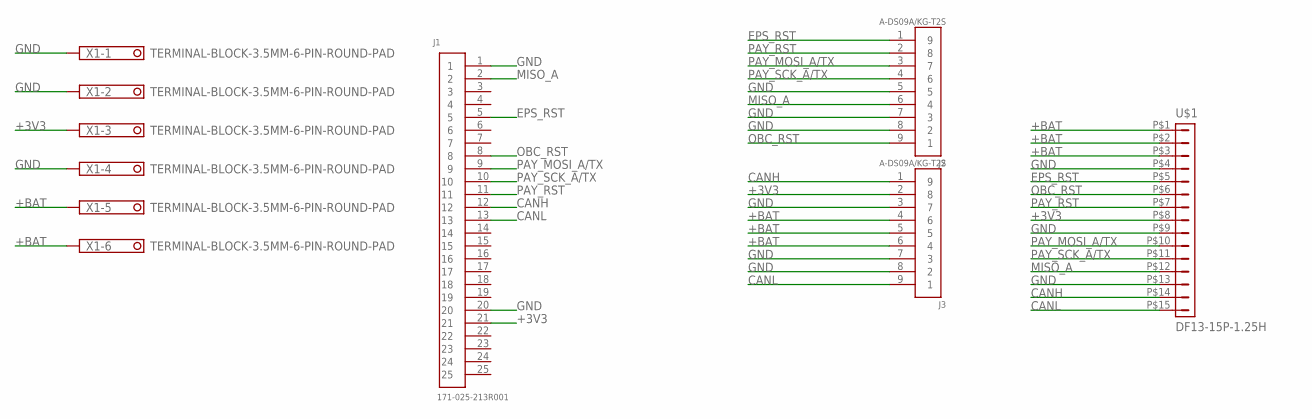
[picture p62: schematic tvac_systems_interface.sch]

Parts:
J1: 171-025-213R001
J2, J3: A-DS09A/KG-T2S
U$1: DF13-15P-1.25H; DF13A-15P-1.25H
X1: TERMINAL-BLOCK-3.5MM-6-PIN-ROUND-PAD; TERMINAL-BLOCK-6-PIN-3.5MM-ROUND-PAD

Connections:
+3V3: J1.21, J3.2 (8), U$1.P$8 (8), X1.3
+BAT: J3.4 (6), J3.5, J3.6 (4), U$1.P$1 (1), U$1.P$2 (2), U$1.P$3 (3), X1.5, X1.6
CANH: J1.12, J3.1 (9), U$1.P$14 (14)
CANL: J1.13, J3.9 (1), U$1.P$15 (15)
EPS_RST: J1.5, J2.1 (9), U$1.P$5 (5)
GND: J1.1, J1.20, J2.5, J2.7 (3), J2.8 (2), J3.3 (7), J3.7 (3), J3.8 (2), U$1.P$4 (4), U$1.P$9 (9), U$1.P$13 (13), X1.1, X1.2, X1.4
MISO_A: J1.2, J2.6 (4), U$1.P$12 (12)
OBC_RST: J1.8, J2.9 (1), U$1.P$6 (6)
PAY_MOSI_A/TX: J1.9, J2.3 (7), U$1.P$10 (10)
PAY_RST: J1.11, J2.2 (8), U$1.P$7 (7)
PAY_SCK_A/TX: J1.10, J2.4 (6), U$1.P$11 (11)

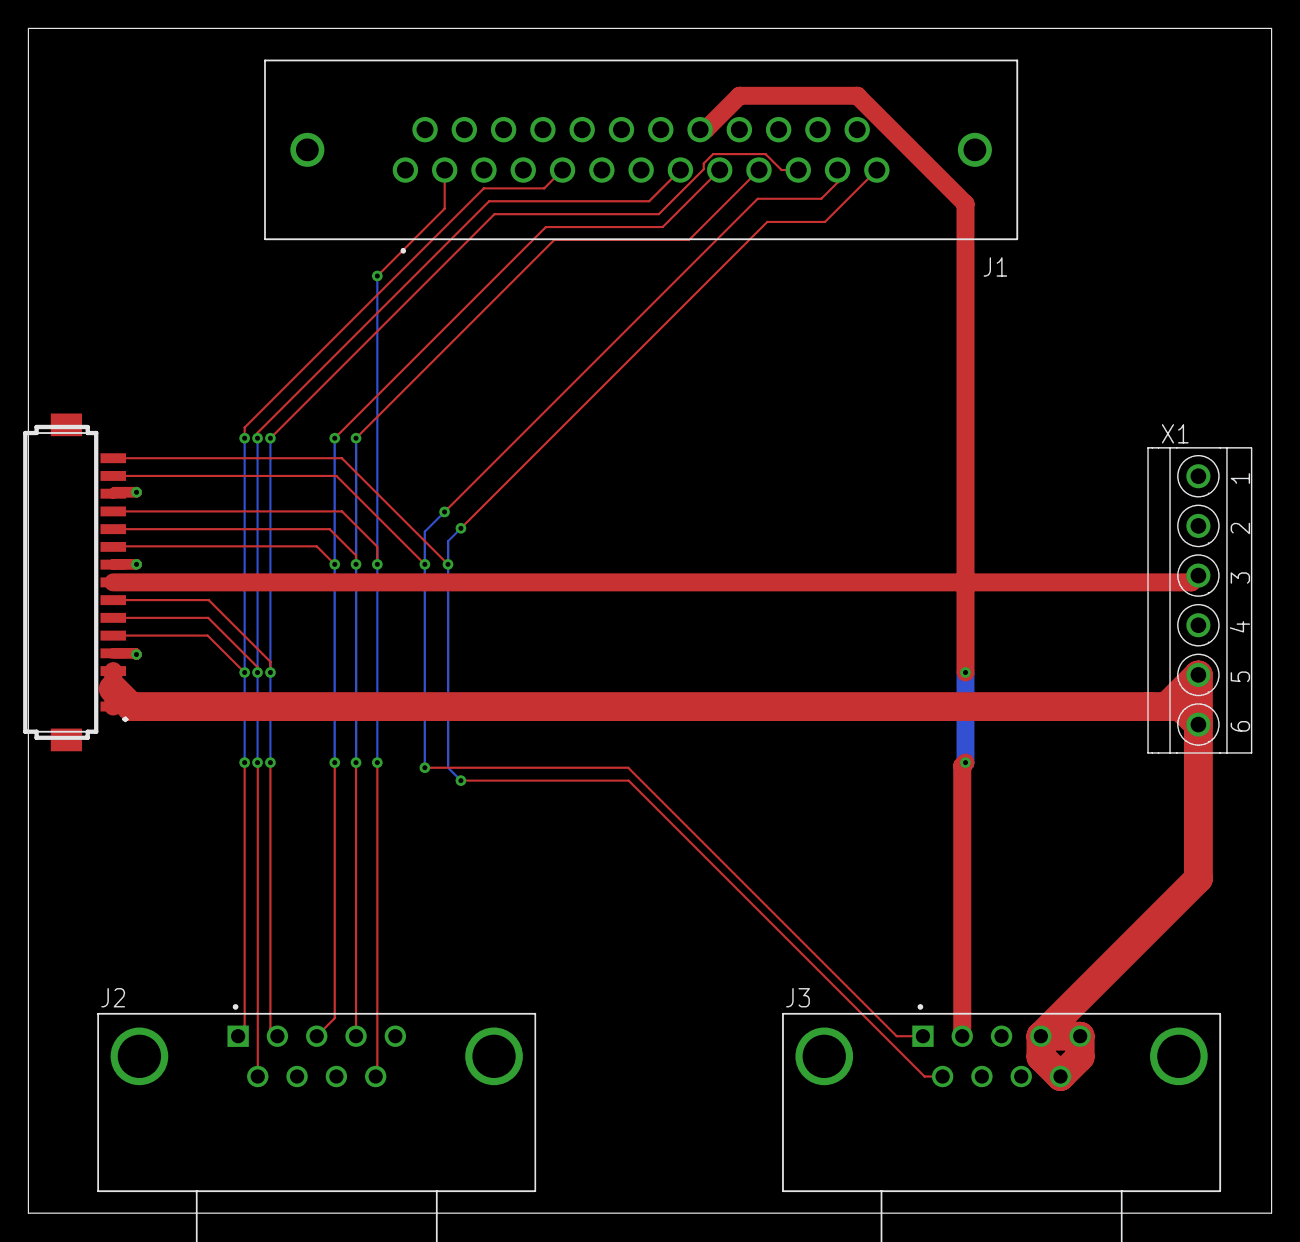
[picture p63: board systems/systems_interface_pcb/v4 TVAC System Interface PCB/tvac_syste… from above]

Board: 2 copper layers, 87.6 x 83.5 mm, 5 parts (0 on the bottom side), 11 nets.

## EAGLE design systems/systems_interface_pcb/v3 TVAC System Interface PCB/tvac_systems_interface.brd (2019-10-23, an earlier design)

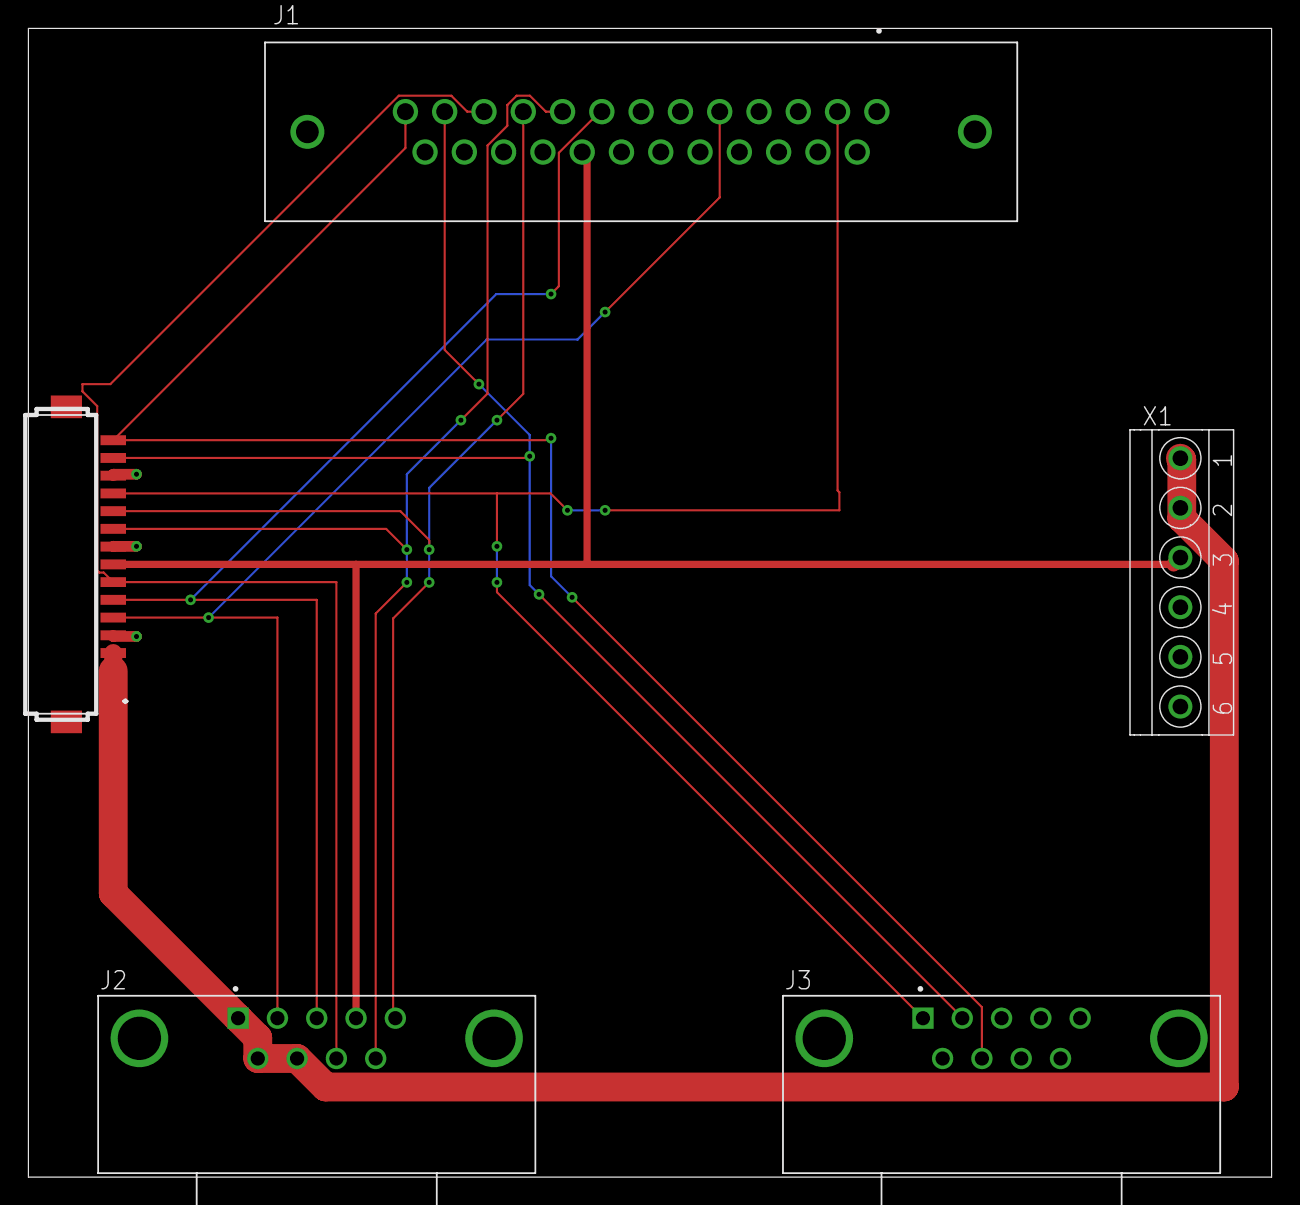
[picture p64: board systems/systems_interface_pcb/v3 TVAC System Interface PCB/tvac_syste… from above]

Board: 2 copper layers, 87.6 x 81.0 mm, 5 parts (0 on the bottom side), 11 nets.

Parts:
J1: 171-025-213R001
J2, J3: A-DS09A/KG-T2S
U$1: DF13-15P-1.25H; DF13A-15P-1.25H
X1: TERMINAL-BLOCK-3.5MM-6-PIN-ROUND-PAD; TERMINAL-BLOCK-6-PIN-3.5MM-ROUND-PAD

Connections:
+3V3: J1.21, J2.4, U$1.P$8, X1.3
+BAT: J2.1, J2.8, J2.9, U$1.P$1, U$1.P$2, U$1.P$3, X1.1, X1.2
CANH: J1.12, J3.2, U$1.P$14
CANL: J1.13, J3.8, U$1.P$15
EPS_RST: J1.5, J2.2, U$1.P$5
GND: J1.1, J1.20, J3.9, U$1.P$4, U$1.P$9, U$1.P$13, X1.4, X1.5, X1.6
MISO_A: J1.2, J3.1, U$1.P$12
OBC_RST: J1.8, J2.3, U$1.P$6
PAY_MOSI_A/TX: J1.9, J2.6, U$1.P$10
PAY_RST: J1.11, J2.7, U$1.P$7
PAY_SCK_A/TX: J1.10, J2.5, U$1.P$11

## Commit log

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2018-04-28 fixed obc hierarchy
    [bus-main.SchDoc, obc_32m1.SchDoc, obc_main_3.0.SchDoc]
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2018-05-05 Added 2nd 5V Boost
    Components still need annotating. New schematic can be entered but might be in the wrong spot for file management shenanigans.
    [eps_6.0.SchDoc, eps_bt2.SchDoc, obc-comm.PrjPcb]
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2018-05-07 eps digital interfaces, fixes
    still need to add eps footprints that are missing, and the pc104 stack!
    [bus-main.SchDoc, eps_32m1.SchDoc, eps_6.0.SchDoc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]
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2018-05-13 fixed all footprint inconsistencies
    should be good to start layout now
    [bus-main.SchDoc, eps_32m1.SchDoc, eps_adc.SchDoc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]
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2018-06-07 Placed everything on the board
    First draft of the layout done? Criticism to follow is welcome. There was a room way out in the distance that was causing room errors earlier.
    [pay-ssm.PcbDoc]
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2018-06-12 Revert "latest version"
    [PC-104 16 bit bus.PCBDOC, PC-104 16 bit bus.schdoc, bus-main.SchDoc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]
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2018-08-04 Switch schematics on 32M1s fixed, added 4 models to Altium PAY PCB Library
    [ATmega32M1.SchDoc, eps_32m1.SchDoc, obc_32m1.SchDoc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]
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2018-08-19 Finishing up the payload schematic changes adding documentation - Finished up document numbering - Finished top level table of contents - Fixed all compilation-time errors - Added preliminary documen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
    [adc-ic.SchDoc, analog-to-digital-stage.SchDoc, dac-ic.SchDoc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]
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2018-08-21 Added New Folder for EPS Schematics
    Added New Folder for EPS Schematics as EPS will have it's own board. Currently running through the compiled errors on the schematic.
    List of error editing I have done so far:
    Folder: eps_6.0.SchDoc
    Error: Net 3V3VOUT1 contains multiple Output Sheet Entrys (Sheet Entry U_eps_bb2-3V3VOUT2(Output))
    Description: There are multiple outputs sheets with one input. (No 1:1 relationship between input and output) (Could that be dangerous?)
    Fix: I assumed that this schematic is correct, I added a no ERC directive
    Error: Net VOLT5VA contains multiple Output Sheet Entrys (Sheet Entry U_eps_bt2-VOLT5VB(Output))
    Description: There are multiple outputs sheets with one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
    [bus-main.SchDoc, eps_32m1.SchDoc, eps_6.0.SchDoc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]
2018-08-21 Revert "Merge branch 'master' of https://github.com/HeronMkII/pcbs"
    This reverts commit f13d3ebe03662746ad973706da83f18dc5279f71, reversing
    changes made to 8b982475518dc3f242ffcc882ecb67a5c11363f1.
    [SolarPanels.PcbDoc, SolarPanels.PcbLib, SolarPanelsAltium.SchDoc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]
2018-08-22 Some CAD DFN Low Noise 3V Ref
    [obc-comm v2.PrjPCB, obc_32m1 (1).SchDoc, obc_can_transceiver (1).SchDoc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]
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2018-09-08 Fixed issues and re-layout pcb for systems debug board
    [syspcb.PcbDoc, syspcb.PrjPCB, syspcb.SchDoc]
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2018-09-15 Updated sys debug pcb as in Issue #31
    [syspcb.PcbDoc, syspcb.SchDoc]
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2018-09-18 Created PAY-LED BOM doc
    - Also fixed opening errors about missing libraries.
    [Bill of Materials-pay-led-pcb.xlsx, pay-led-pcb.PrjPCB, pay-optical.PrjPCB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]
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2018-09-23 Systems wiring diagram v0.3
    - CAN bus terminations
    - EPS battery and solar panel connections
    - Fixed some of header orientations
    [eps.SchDoc, eps_obc_pay_sys.SchDoc, obc.SchDoc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]
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2018-09-24 Replaced old version of EPS on master with version from epsV2 branch
    Trying to avoid merge conflicts so bringing over the newest folder version. Hoping this doesn't cause further problems.
    [bt_current_monitor.SchDoc, bus-main.SchDoc, eps.PcbDoc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]
2018-09-24 Misc error fixes for bus-eps
    [bt_current_monitor.SchDoc, eps_6.0.SchDoc, eps_bt1.SchDoc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]
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2018-09-26 Updated libraries and pcbs-common submodule
    - Created drop-in replacements for pushbutton and LED so that our 0603
    LED footprint and pushbutton footprint would compile with heron-general.
    - Updated the pcbs-common version
2018-09-27 Reworking EPS schematic design and mapping schematics to footprints
    Implementing pcbs-common subsheets into the design - much rework in progress
    [eps.PcbDoc, eps_32m1.SchDoc, eps_adc.SchDoc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]
2018-09-28 Implemented pcbs-common sheets in EPS schematic
    Introducing the pcbs-common sheets has invariably produced a number of errors (see below):
    - compiler is mad at PEX for having I/O on only I and O ports
    - sheet entries are not matched to ports (very interesting considering their connections are placed right on top of eachother)
    - there are a number of pins I currently have no ERC'd (32m1 pins, PEX, CAN reset [which I suspect needs connection to 32m1])
    [bt_current_monitor.SchDoc, bus-main.SchDoc, eps_6.0.SchDoc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]
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2018-09-29 added in RUN<->PGM switches and fixed changes as in Issue #31
    [syspcb.PcbDoc, syspcb.PrjPCB, syspcb.SchDoc]
2018-10-03 Reworked Errors on EPS Schematic after pcbs-common Integration
    Still problems with converting the schematic to the layout; cannot find classes and pins undefined.
    Shematic will need a debugging header added, LED buffer, etc.
    [bt_current_monitor.SchDoc, bus-main.SchDoc, eps.PcbDoc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]
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2018-10-03 Connected all PWR and fix problems as in Issue #31
    [syspcb.PcbDoc]
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2018-10-06 Added missing footprints
    [bus-main.SchDoc]
2018-10-06 Added Remaining Footprints
    RBF pin is the only missing footprint
    [bt_current_monitor.SchDoc, eps_batt.SchDoc, eps_bb1.SchDoc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]
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2018-10-08 Organizing/Minor Routing of EPS Rooms
    Still need to import some components eg. PEX from the schematic but encountering many errors when trying this, not sure of the cause.
    [bt_current_monitor.SchDoc]
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2018-10-10 Added footprints and imported into layout
    This reduced the number of errors by a lot (like 80%), but there seems to be a problem with saving the footprint libraries. Dylan please check!!!!!
    [eps.PrjPCB, eps_batt.SchDoc, eps_pv.SchDoc]
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2018-10-30 OBC schematic fixes
    [micro-circuit-ATMEGA32M1.SchDoc, obc-comm.PrjPCB, obc_flash.SchDoc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]
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2018-11-03 OBC layout fixes, error free
    [eps.PrjPCB, obc-comm.PcbDoc, obc-comm.PrjPCB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]
2018-11-05 Added EPS Thermistor voltmeters and new battery connector
    We have a bunch of components that still need values. I've also had to add the pcbs-common sheets to the EPS project every time I've pulled, not sure on what end this is a problem.
    [bt_current_monitor.SchDoc, bus-main.SchDoc, eps.PrjPCB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]
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2018-11-07 Fixed footprints
    Still need to check battery and pv connectors
    [bt_current_monitor.SchDoc, eps.PrjPCB, eps.SchDoc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]
2018-11-09 Reformatting, fixed wiring bug in PV
    [bt_current_monitor.SchDoc, bus-main.SchDoc, eps.PrjPCB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]
2018-11-10 Replaced pv connectors with 4-pos picoblade
    [eps.PrjPCB, eps_bt1.SchDoc, eps_digital.SchDoc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]
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2018-11-15 EPS Laid Out (Rough draft)
    A few notes from this session:
    - need to check the height of components under OBC
    - need some footprints changed, namely the BATT connector and battery holder
    - need to check how sensitive the IMU is to converter noise
    - need to work out spacing on the bottom for programming headers, pins, LEDs
    - need to finalize the location of the butterfly connectors
    [eps_digital.SchDoc]
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2018-11-23 Routing + misc. fixes
    - Refixed the two deployment switches (they hadn't commited properly last time)
    - Routed boost converter 2
    - Removed -PACK port from eps_digital because the ADC didn't have enough pins. From eps_batt the port is grounded
    [eps.PrjPCB, eps.SchDoc, eps_batt.SchDoc]
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2018-11-29 Fixing flash layout OBC
    [obc-comm.PcbDoc, obc_rtc.SchDoc]
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2018-12-01 Misc. routing
    - Swapped boost converter voltage/current (formerly pins 15 and 16) with pack voltage/current (formerly pins 7 and 8) on the ADC, for board location reasons
    - Connected THM1 and THM2 to ATMEGA
    - Set up pours for +5V, DEPSWITCH2, and RBL
    [eps_digital.SchDoc]
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2018-12-01 *Tried* making a bus for LED buffer, fixed butterfly positions
    [obc-comm.PcbDoc]
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2018-12-05 Fixed molex footprint
    [eps_batt.SchDoc]
2018-12-05 Revert "Merge branch 'master' of https://github.com/HeronMkII/pcbs"
    This reverts commit 21289adaa545611b1161b36b688d4a374fd72185, reversing
    changes made to 309508f7533e297b506bb766bb7fd3f1eab5486a.
    [obc-comm.PcbDoc]
2018-12-05 Revert "Fixed molex footprint"
    This reverts commit 309508f7533e297b506bb766bb7fd3f1eab5486a.
    [eps_batt.SchDoc]
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2018-12-06 Fixed misc schematics
    Currently experimenting with VCC pour positioning
    [eps.PrjPCB, eps_batt.SchDoc, eps_digital.SchDoc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]
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2018-12-08 fixed the pour issue
    [syspcb.PcbDoc]
2018-12-08 Fixes
    - Merged boost converter current monitor back into sheet
    - BT sense resistor changed from 1mΩ to 10 mΩ
    - Renamed intermediate nets between batteries, deployment switches, and RBL pin
    - Input power rework in progress
    [Bill of Materials-eps.csv, Bill of Materials-eps.xls, bt_current_monitor.SchDoc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]
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2018-12-12 Some fixes, started placing silk screen
    [obc-comm.PcbDoc]
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2018-12-21 Routing fixes
    [obc-comm.PcbDoc, obc-comm.PrjPCB, obc_comm.PcbDoc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]
2018-12-21 Butterflies fixed, misc routing
    [obc-comm.PrjPCB, obc_comm.PcbDoc, obc_rtc.SchDoc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]
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2018-12-23 Wiring diagram v0.9.1 - flipped Molex battery connector on SYS, SYS CAN placement
    [can.SchDoc, sys.SchDoc, systems_wiring_diagram.PrjPCB]
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2018-12-30 Corrected 32m1 crystal routing
    [bus-main.SchDoc]
2018-12-30 Routed thicker traces for 5V and other fixes
    [bus-main.SchDoc, eps_batt.SchDoc, eps_bb.SchDoc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]
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2019-01-01 Fixed current monitoring references as per GitHub comments
    [eps_batt.SchDoc, eps_digital.SchDoc, eps_pv.SchDoc]
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2019-01-01 Correctly linked OBC to pcbs-common, fixed issues which arose
    [obc-comm.PrjPCB, obc_comm.PcbDoc, obc_flash.SchDoc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]
2019-01-01 Fixed gate drive buffer configuration, butterfly connections for systems wiring diagram v0.9 compliance
    [eps_pv.SchDoc]
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2019-01-03 fixed some pcb labelling issues
    [syspcb.PcbDoc, syspcb.PrjPCB]
2019-01-03 Corrected outstanding SYS-PCB errors. Should be ready to send out.
    [syspcb.PcbDoc, syspcb.PrjPCB]
2019-01-03 Fixed OBC butterfly orientations
    [obc_comm.PcbDoc]
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2019-01-04 Fixed outstanding issues with OBC, aesthetic updates to systems
    [obc-comm.PrjPCB, obc_comm.PcbDoc, obc_flash.SchDoc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]
2019-01-04 fixed things as pointed in Issue #31
    [syspcb.PcbDoc]
2019-01-04 OBC Silkscreen placed, PGM-RST switch flipped
    [obc-comm.PrjPCB, obc_comm.PcbDoc]
2019-01-05 Added +5V to debug header and fixed outstanding issues
    [obc_comm.PcbDoc, obc_main_3.0.SchDoc]
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2019-01-15 BOM update
    Fixed quantity section
    [eps_bom_JAN2019.xlsx, eps_bom_JAN_2019.xlsx]
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2019-05-09 Fixed pushbutton issue on System Debug PCB and Panel +/- label
    [syspcb.PcbDoc, syspcb.PrjPCB]
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2019-05-24 Routed deployment switch prototype PCB
    No debugging headers anywhere currently. Hopefully didn't mess up the libraries.
    [DepSwitches.PrjPCB, dep-switches.PcbDoc, dep-switches.SchDoc]
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2019-05-25 Fixed broken pcbs-common links and have all components placed
    [motor-driver.SchDoc, pay-motors-control.PrjPCB, pay-motors-prototype.PcbDoc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]
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2019-05-29 Revert "Testing my github"
    This reverts commit b73e565350286edc6b3f27a43d5a1d34e1d43d15.
    [Batt_Protection.SchDoc]
2019-05-29 Added reverse bias diode to dep switch prototype schematic
    Same diode as in the EPS PV sheet. Still need to add zener diode
    [dep-switches.SchDoc]
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2019-05-29 Added motorRegular prototype schematic, respecing footprints for layout/routing due to previous incompatibility
    [30V Output Design.schdoc, 30V Sample Layout.PcbDoc, 40V Output Design.schdoc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]
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2019-05-31 Minor Changes to Battery Protection IC
    fixed some footprints
    [Batt_Protection.PcbDoc]
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2019-05-31 Deployment Switches PCB is done, just waiting on selecting reverse voltage and over-voltage diodes
    [dep-switches.PcbDoc, dep-switches.SchDoc, eps.PrjPCB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]
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2019-06-01 Added rule file and fixed routing
    [Batt_Protection.PcbDoc, Batt_Protection.SchDoc]
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2019-06-01 Added components to heron libraries, fixed career-ending error where both load switches were pointing in the same direction
    [DepSwitches.PrjPCB, dep-switches.PcbDoc, dep-switches.SchDoc]
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2019-06-02 Fixed silk screen and add in bulk bypass caps
    [pay-motors-prototype.PcbDoc]
2019-06-02 Renamed schematic components and fixed some routing, added 3-4.2V & 28V voltage labellings beside headers
    [30V Output Design.schdoc, motorRegulator.PcbDoc]
2019-06-02 Added test pads, fixed some silk screen issue
    [pay-motors-prototype.PcbDoc, pay-motors-prototype.SchDoc]
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2019-06-02 Fixed some issues, started re-routing for 64m1 signals
    [pay-motors-prototype.PcbDoc, pay-motors-prototype.SchDoc]
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2019-06-04 Fixed Issues spotted by Dylan, ready for DRC
    [pay-motors-prototype.PcbDoc, pay-motors-prototype.SchDoc]
2019-06-04 Final fixes
    [28V-motor-driver.SchDoc, pay-motors-prototype.PcbDoc]
2019-06-04 Fixed resistors and BOM, added properly rated output caps, re-routed
    [2019-06-03_23-23-21.PcbLib, 2019-06-03_23-23-21.SchLib, 2019-06-04_00-23-30.PcbLib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]
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2019-06-04 Some routing/pours fixing, added logo
    [motorRegulator.PcbDoc]
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2019-06-10 fixed issues with motor prototype and re-exported gerbers
    [4-layer.DRL, 4-layer.GBL, 4-layer.GBO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]
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2019-06-15 Changed to correct packaging for pay-motors BOM
    [28V-motor-driver.SchDoc, pay-motors-prototype.SchDoc]
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2019-06-16 Finished Prototype BOM (One item still needs fixing)
    [Batt_Protection.SchDoc, Battery_Protection.PrjPCB]
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2019-06-17 Fixed BOM and re-exported as xlsx file for pay-motors
    [28V-motor-driver.SchDoc, Bill of Materials-pay-motors-control.xlsx, pay-motors-prototype.SchDoc]
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2019-06-23 Rerouted TX and RX CAN, H1 and H2 swap is underway
    [boost.SchDoc, buck_boost.SchDoc]
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2019-07-15 replaced pay-optical with v3, started new pay-led-v3, added LO P47K LED to Heron General
    [ATMEGA8A.SchDoc, Bill of Materials-pay-led-pcb.xlsx, Bill of Materials-pay-optical.xls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]
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2019-07-17 pay-ssm schematics semantics fix
    [pay-ssm.SchDoc, thermal-system-overview.SchDoc, thermistors-heaters-connectors.SchDoc]
2019-07-17 motor driver fix
    [motor_control.SchDoc]
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2019-07-18 Updates OBC schematics to pcbs-common and fixed net/port errors
    [obc-comm.PrjPCB, obc_main_3.0.SchDoc]
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2019-07-18 Revert "Minor changes to schematics from tweaking"
    This reverts commit c7ebd96822540cc2d848a2b22977b13b59429b38.
    [batt.SchDoc, buck_boost.SchDoc, bus-main.SchDoc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]
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2019-07-19 pay-ssm top level fixes
    [boost-converter.SchDoc, motor_control.SchDoc, motors-overview.SchDoc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]
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2019-07-20 Re-did OCB top layer, grouped SPI devices, fixed 28 V MOSFET wiring :(
    [30V Output Design.schdoc, obc.PcbDoc, obc_main_3.0.SchDoc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]
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2019-07-21 Added TPS25982 schematic symbol. Didn't mess up pin numbering this timr :)
    [TPS25982.SchLib, current-limiter.SchDoc, main.SchDoc]
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2019-07-21 Thermal system ADCs signals fixes, heater ctrl minor fixes
    [boost-converter.SchDoc, heaters-connectors.SchDoc, pay-ssm.SchDoc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]
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2019-07-24 New transceiver/EPS circuit corrected and confirmed by Bruno
    [main.SchDoc]
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2019-07-24 MCU signal fixes
    [optical-connection.SchDoc, pay-ssm.SchDoc, thermal-system-overview.SchDoc]
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2019-07-25 trying to fix git
    [ADC Breakout.SchDoc, DRV8834.SchDoc, Heater Control.SchDoc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]
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2019-07-26 Revert "Annotated rest of schematics"
    This reverts commit fd5b5ffe3535dc3bf94b7089d43ff6bf077e4abe.
    [boost.SchDoc]
2019-07-26 Revert "Revert "Annotated rest of schematics""
    This reverts commit 8ac278deaf0db5107791f22e527b567bf4704532.
    [boost.SchDoc]
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2019-07-26 [SYS] Reorganize and clean up schematic hierarchy, import into layout
    When updating schematics to PCB layout:
    - Had some missing errors with unmatched nets and missing footprints
    - Some components got removed from the layout and put to the side, will fix this later
    [eps_power.SchDoc, programming.SchDoc, syspcb.PcbDoc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]
2019-07-26 fixed motors ctrl signals, changed sensors, annotated everything
    [DRV8834.SchDoc, Heater Control.SchDoc, Heater Power.SchDoc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]
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2019-07-26 Fixing compilation errors in progress
    [ADC Breakout.SchDoc, Heater Control.SchDoc, Heater Power.SchDoc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]
2019-07-26 Fixed all compilation errors but one, restarting pay-ssm layout
    [ADC Breakout.SchDoc, ADC-Breakout.SchDoc, DRV8834.SchDoc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]
2019-07-26 fixing merge conflicts
    [ADC Breakout.SchDoc, ADC-Breakout.SchDoc, DRV8834.SchDoc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]
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2019-07-26 Re-fixed compilation errors (changes got discarded during merge, thanks git)
    [ADC Breakout.SchDoc, Heater Control.SchDoc, Heater Power.SchDoc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]
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2019-07-26 Fixed pay-ssm annotation error for the ADS7952
    [ADC Breakout.SchDoc, DRV8834.SchDoc, Heater Control.SchDoc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]
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2019-07-26 Fixed title block revision for schematics
    [ADC Breakout.SchDoc, DRV8834.SchDoc, Heater Control.SchDoc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]
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2019-07-27 [SYS] Remove duplicate programming schematics, fix rooms, cleanup
    [buffered_leds.SchDoc, programming.SchDoc, syspcb.PcbDoc]
2019-07-27 [SYS] Start fixing PCB rooms and component placement
    [syspcb.PcbDoc, syspcb.PrjPCB]
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2019-07-28 [PAY-SSM] jk I was wrong before, re-layout VCC plane done
    [Heater Power.SchDoc, Motors.SchDoc, TOP.SchDoc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]
2019-07-28 [SYS] Use common LEDs sheet, fix net naming and footprints
    [buffered_leds.SchDoc, eps_power.SchDoc, programming.SchDoc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]
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2019-07-28 [SYS] Fix pcbs-common component associations
    [eps_power.SchDoc, programming.SchDoc, syspcb.PcbDoc]
2019-07-28 [SYS] Fix outjob
    [syspcb.PrjPCB]
2019-07-28 [SYS] Add back battery DF13, fix solar terminal orientation on silkscreen
    [eps_power.SchDoc, syspcb.PcbDoc, syspcb.PrjPCB]
2019-07-28 [SYS] Recreate syspcb.SchDoc to fix lag
    [syspcb.PcbDoc, syspcb.PrjPCB]
2019-07-28 [SYS] Fix designators and rooms
    [programming.SchDoc, syspcb.PcbDoc, syspcb.PrjPCB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]
2019-07-28 [SYS] Start new layout, fix programming silkscreen/placement
    [syspcb.PcbDoc, syspcb.PrjPCB]
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2019-07-31 [PAY-SSM] Fixed thermistors and adc signals issue
    [MF Thermistors.SchDoc]
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2019-08-01 Many reverts and discarded commits
    This reverts commit ce1502eba7764bf8672427c12b6a89dbe00698e4.
    [MF Thermistors.SchDoc]
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2019-08-03 [SYS] Flip batt connector, reorganize power debug header, placement changes
    [eps_power.SchDoc, syspcb.PcbDoc]
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2019-08-04 [SYS] Reorganize debug headers, fix DSUB footprint, change LED resistances
    [eps_power.SchDoc, syspcb.PcbDoc, syspcb.SchDoc]
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2019-08-04 [SYS] Major redesign of layout placement
    [syspcb.PcbDoc]
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2019-08-04 properly fixed the inductor footprint by re-linking
    [Heater Power.SchDoc]
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2019-08-04 [SYS] Swap batt screw terminal pins
    [eps_power.SchDoc, syspcb.PcbDoc, syspcb.SchDoc]
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2019-08-07 [SYS] Replace batt connector, label 3V3 releases, remove RTC LED
    [eps_power.SchDoc, programming.SchDoc, syspcb.PcbDoc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]
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2019-08-07 [PAY-SSM] Fixed annoying textboxes in schematics
    [TOP.SchDoc, sensors.SchDoc]
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2019-08-09 [SYS] Fix some DRC errors for unrouted nets
    [syspcb.PcbDoc, syspcb.PrjPCB]
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2019-08-10 [OBC] Finished routing, no DRC unrouted net errors
    [obc-comm.PcbDoc]
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2019-08-11 [SYS] Fix pour dimensions and DRC errors, add antenna warning on silkscreen
    [syspcb.PcbDoc]
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2019-08-11 [PAY-SSM] fixed boost connections, relayout high-power
    [Heater Power.SchDoc, boost-converter.SchDoc]
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2019-08-15 Exported gerber files, fixed bypassing, silk screen resizing, tinting vias
    [obc-comm.GBL, obc-comm.GBO, obc-comm.GBP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]
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2019-08-15 [PAY-SSM] corrected the silkscreen for gerber files
    [pay-ssm-v4-2.GBL, pay-ssm-v4-2.GBO, pay-ssm-v4-2.GBP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]
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2019-08-16 [SYS] Fix project file associations with consistent naming, delete outdated files
    [systems_pcb.PrjPCB]
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2019-08-17 [OBC] Silkscreen and misc fixes
    [boost.SchDoc, obc_main_3.0.SchDoc]
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2019-08-18 [SSM] flipped thermistors connectors, other minor changes
    [TOP.SchDoc]
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2019-08-20 [OBC] Repositioned programming headers to not crash into EPS, rerouted, generated new gerbers/NCDrill
    [obc-comm.GBL, obc-comm.GBO, obc-comm.GBP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]
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2019-08-24 [SYS] Swap CANH and CANL on buffer, finish CAN LED routing changes
    [systems_pcb.SchDoc]
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2019-08-25 [EPS] Added missing schematic documents from pcb-common
    I was missing links to pcb-common schematics - Recently just added them back in
    [eps.PrjPCB]
2019-08-25 Revert "[EPS] Added missing schematic documents from pcb-common"
    This reverts commit 51fe834553e9f224018b54543928230efe04461c.
    [eps.PrjPCB]
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2019-08-25 Revert "[EPS] re-annotated components"
    This reverts commit 076b4c02185c593a30c8d283738f20736dbbc667.
    [batt.SchDoc, eps.PrjPCB]
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2019-08-25 [EPS] Fixed Title blocks to match function
    [dep-switches.SchDoc, heaters-sensors.SchDoc, solar.SchDoc]
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2019-08-25 [EPS] Fixed some text, added test points
    Test points added to:
    - Boost
    - Batt pro
    [boost.SchDoc]
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2019-08-26 [SSM] break out boost EN pin, add BATT volt mon, some other minor fixes
    [DRV8834.SchDoc, Heater Power.SchDoc, TOP.SchDoc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]
2019-08-26 [OBC] Re-routed butterfly, MCU bus, LEDs, spi-i2c, fixing up last set of DRC errors
    [obc-comm.PcbDoc, obc_main_3.0.SchDoc]
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2019-08-26 Fixed remaining DRC errors on OBC, changed all passives to heron general footprints
    [obc-comm.PrjPCB, obc_flash.SchDoc, obc_main_3.0.SchDoc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]
2019-08-26 [EPS] addes preliminary DF13/Load switch RBF replacement
    [batt.SchDoc]
2019-08-27 [EPS] Corrected DF13 RBF replacement based on Dylan's input. Added damped RL series filter for SMPS
    [batt.SchDoc, eps.PrjPCB, heaters-sensors.SchDoc]
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2019-08-27 [SSM] fixed most motors bus
    [TOP.SchDoc]
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2019-08-28 Re-routed DF13, fixed some DRCs, 5 remaining, specd filter parts
    [batt.SchDoc]
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2019-08-29 [SYS] Fix schematic title blocks, embed CAN logic voltage image
    [can_comparators.SchDoc, eps_power.SchDoc, programming.SchDoc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]
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2019-08-29 [EPS] Added pin 1 to SN74LV1 symbols, made TC7WB67 symbol and replaced it, configured it to active high, replaced pull up with pull down, finally found that shelved polygon DRC error
    [batt.SchDoc, dep-switch-TPS22959DNYT.SchDoc, eps.SchDoc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]
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2019-08-30 [EPS] Fixed SCHEMATIC of RBF
    PCB still needs fixing
    [batt.SchDoc]
2019-08-30 [EPS] minor fix to RBF schematic
    [batt.SchDoc]
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2019-08-30 [EPS] reworked RBF load switch to fit new net names
    [batt.SchDoc, dep-switches.SchDoc]
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2019-08-31 [OBC] Misc DRC and silkscreen fixes, cleanup
    [obc_flash.SchDoc, obc_main.SchDoc, obc_rtc.SchDoc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]
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2019-09-01 [OBC] Misc routing fixes
    [obc.PrjPCB]
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2019-09-03 [OBC] Improve CAN transceiver layout from datasheet guide, misc layout fixes
    [obc.PrjPCB]
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2019-09-03 [EPS] routing fixes from review and new exports
    [eps-flight.GBL, eps-flight.GBO, eps-flight.GTL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]
2019-09-04 [SYS] Fix outjob for BOM
    [systems_pcb.PrjPCB]
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2019-09-06 [SSM] Finished fixing some logic power paths
    [Heater Control.SchDoc, MF Thermistors.SchDoc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]
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2019-09-09 [SSM] more tweaking, fixed heater LEDs
    [Heater Control.SchDoc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]
2019-09-09 [SSM] heaters LED fixes
    [Heater Control.SchDoc, pay-ssm.PrjPCB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]
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2019-09-11 [SSM] Updated board size, fixed DRC, updated gerbers
    [pay-ssm-v4-4.GBL, pay-ssm-v4-4.GBO, pay-ssm-v4-4.GBP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]
2019-09-11 [SSM] fix close drill hits, fixed DRC, re-exported gerbers
    [pay-ssm-v4-4.GBL, pay-ssm-v4-4.GBO, pay-ssm-v4-4.GBP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]
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2019-09-13 [SSM] fix route tool path
    [pay-ssm-v4-4.GBO]
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2019-09-26 [PAY] limit switch redesign and project outputs
    [pay-lim-switch-1.PcbDoc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]
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2019-10-02 [EPS] BOM fixes and re-export
    [eps-BOM-20191002.xls, flight-BOM_2019-09-19.xlsx, flight-BOM_2019-10-02.xlsx]
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2019-10-28 flipped D25 so cable is plugged into side of board
    [copper_bottom.gbr, copper_top.gbr, drill_1_16.xln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]
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2020-01-14 [SSM] boost converters volt div res value correction
    [Boost Converter 10V.SchDoc, Boost Converter 6V.SchDoc]
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
